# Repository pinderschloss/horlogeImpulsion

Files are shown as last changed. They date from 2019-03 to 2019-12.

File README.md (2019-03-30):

https://bit.ly/2SEGcSN
# horlogeImpulsion
Contrôleur d'horloge fille à impulsion, en subsitution à une horloge mère. Permet, selon les configurations, le pilotage par une boitier autonome alimenté par pile, batterie, ou port USB.
Il est conçu autour:
- d'un programme dont les options de compilation doivent être adaptées au besoin,
- et d'un circuit imprimé unique sur lequel l'implémentation des composant varie en fonction des besoins.

Convient (testé) pour:
- Brillié 'rosace 10 ohms' à impulsions électriques alternées (2 impulsions par minute) sur 2 piles AA, soit en pas simples toutes les 30secondes, soit en double pas toutes les minutes.
- Bodet '24V' à impulsions électriques alternées (1 impulsion par minute) sur alimentation USB.
- IBM '24V' à impulsions électriques non-alternées sur alimentation USB. 

Devrait convenir pour:
- Tout type d'horloge fille à impulsions alternée ou non, nécessitant une tension entre 2 et 36V, sur tout type d'alimentation entre 2 et 5V.

## Description :
Le controleur se base sur:
- une base de temps électronique (RTC : real time clock).
- une alimentation - n’importe quelle source délivrant entre 3V et 5V continu.
- un microcontroleur ATTinyx5 (25, 45 ou 85; testé uniquement sur Attiny85)

## Composants :
1.	Platine
2.	Microcontrôleur ATTINYx5-20PU (testé sur ATTINY85-20PU)
3.	Module RTC (la pile est facultative et ne sert pas) - testé sur un DS3231
4.	Boitier de pile ou alimentation microUSB
5.	Bouton poussoir de réglage
Selon les versions/besoin:
6.	Interrupteur ON/OFF 
7.	Pont en H et bornier pour relier la platine à l’horloge (avec sa résistance de 10 ohms)
8. transistor et bornier de sortie directe
9. bornier de sortie pour contrôle d'un pont H extérieur
10. Module convertisseur (élévateur) de tension vers la tension de fonctionnement de l'horloge (généralement 18V ou 24V)

## Brancher la platine à l’horloge :
### Brillié (10Ohms) 
-  Eteindre le contrôleur (interrupteur ON/OFF) ou bien débrancher l'alimentation
-  Relier bornes de sortie de la platine  avec les bornes d’entrée de l’horloge (2 fils). Laisser la résistance de 10ohm qui relie les deux bornes à vis .
-  Fixer l’ensemble des éléments au dos de l’horloge en assurant que l’on puisse manipuler : 
   -  les 2 interrupteurs (ON/OFF et le bouton poussoir AVANCE),
   -  le bouton,
   -  le boitier de piles.
-  Rallumer le contrôleur (interrupteur ON/OFF) ou bien brancher l'alimentation
-  Appuyer plusieurs secondes sur le bouton AVANCE, pour faire avancer l’aiguille des minutes de quelques minutes.
-  Quelques après avoir relâché le bouton AVANCE, regarder la position de l’aiguille des minutes :
   -  Si elle est alignée sur un point du cadran indiquant les minute, passer à l’étape de mise à l’heure.
   -  Sinon, elle se trouve au milieu entre deux points de minutes. Recommencer cette étape de branchement en inversant les deux fils qui relient la platine à l’horloge.

### Horloges à impulsions alternées
- Si la tension requise est supérieure à la tension d'alimentation, relier le pont en H externe (4 fils: VP, GND, S1 et S2) et brancher l'horloge comme une Brillié (10ohms) depuis le pont en H.
- Sinon (pas d'élévation de tension), procéder comme pour les Brillié (10ohms)

### Horloges à impulsions monopôlaires (pas d'inversion de polarité)
Ces horloges peuvent avoir 2 ou 3 fils. La platine peut elle-même comporter un bornier double ou triple. Toutes les combinaisons sont possibles. Attention: ne pas considérer ni connecter le fil de masse de l'horloge.
- S'il y a deux fils: en connecter un sur le connecteur marqué "rouge" (vers le coin de la platine) et l'autre fil dans l'autre bornier (n'importe lequel s'il y en a deux)
- S'il a 3 fils: le fil rouge doit être connecté à la platine sur le connecteur marqué "rouge" (vers le coin de la platine), et les deux autres soit ensemble soit séparemment dans le ou les les autres connecteurs du borniers.
- Lorsqu'on appuie sur le bouton poussoir AVANCE, vérifier que l'aiguille avance bien d'une minute.

## Mettre à l’heure l’horloge
-	Eteindre le contrôleur (interrupteur ON/OFF)
-	Approcher de l’heure réelle à la main, sans la dépasser (environ cinq à dix minutes avant l’heure réelle), en agissant directement sur le mécanisme. Pour cela agir directement sur le mécanisme d'entrainement (dépend du mécanisme - en général on peut l'avance et le reculer avec les deux mains ou tournevis), ou bien allumer le controleur et appuyer sur le bouton AVANCE sans le relacher (la vitesse d'avancement augmente lorsqu'on reste appuyé, mais cette opération peut être un peu fastidieuse).
-  Allumer le contrôleur (interrupteur ON/OFF)
-	En appuyant sur le bouton AVANCE, faire avancer jusqu’à afficher l’heure actuelle. A ce stade, l’horloge a de 0 à 59 secondes de retard.
-	Surveiller le nombre de secondes de l’heure réelle. Entre 55s et 59s, appuyer sur le bouton AVANCE. L’aiguille des minutes passe à la minute suivante: relacher immédiatement.

Note : 
-	 Ce réglage s’effectue de la même façon quel que soit le mode choisi (mode 60 : minute entière, ou mode 30 : demi minute), et se fait sur les minutes entières uniquement.
-	Compte tenu du temps variable de prise en compte de l’appui sur le bouton AVANCE, il est difficile d’obtenir une synchronisation meilleure que 2 secondes.

## Choix du mode de fonctionnement :
Identifier les caractéristiques de l'horloge:
- voltage
- nombre de fils
- type de 'moteur': 
  - électro-aimant et crabot sur roue crantée = impulsions non-alternées (les impulsion alternées fonctionneront aussi)
  - moteur type pendule et mécanisme d'échapement = impulsions alternées
  - moteur type Lavet (pas-à-pas 2 pas) = impulsions alternées
- période : temps minimal entre deux états stables de l'entrainement: 30 secondes ou 60 secondes. A tester à la main.

Attention: pour les horloges de période différentes de 30s ou 60s, il faudra modifier le programme (et pas seulement les options de compilation).

Pour les horloges dont la période est 30s:
- choisir si on souhaite un mouvement toutes les 30 secondes, ou un double mouvement toutes les 60s
- Ce choix n’a pas d’influence sur la précision de l’horloge. Le bruit produit par l’avancée de l’aiguille est différent selon le mode (un ‘clac’, ou bien un double ‘clac’ mais deux fois moins fréquent).

## Préparation de la platine
Voir le BOM.txt

## Programmation du microcontroleur :
- Le code est disponible à l’adresse suivante https://github.com/pinderschloss/horlogeImpulsion/
- Platine et code sont prévus pour fonctionner avec les microcontrôleurs ATTINYx5-20PU (x5 : 25 ou 45 ou 85) d’ATMEL. La consommation d'énergie est réduite autant que possible par une utilisation du mode sommeil autant de possible.
- La programmation du microcontrôleur peut se faire par une carte arduino par exemple (chercher Arduino ISP).
- Attention le microcontroleur ne peut pas être programmé en place sur le circuit imprimé.
- Le code est adaptable pour fonctionner avec des horloges nécessitant des signaux différents, en commentant ou décommentant les options de compilation.

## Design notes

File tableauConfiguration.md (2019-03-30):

# Configuration matérielle et logicielle

Cette partie détaille les différences entre les configurations matérielles pour la platine. La partie commune à toutes les platines est décrite dans BOM.txt. Ce fichier comprend aussi les différents éléments spécifiques listés ci-dessous, mais sans explications.

## Tensions:
Alimentation du module: **Vc** (doit être comprise entre 3V et 5V)
Tension de fonctionnement de l'horloge: **VP** (doit être comprise entre Vc et 36V)

- Si **VP** = **Vc** : pas de module élévateur de tension
- Si **Vc** < **VP** :  prévoir module élévateur de tension *x-tension*

## Connection de l'alimentation:
Si on utilise pour une alimentation qui se termine par deux fils (par exemple un boitier à piles), il faut installer un bornier d'alimentation:
- En général utiliser un bornier double (**GND** / **Vc**),
- Dans le cas d'une horloge à impulsions alternées avec **VP** > **Vc**, prévoir un bornier triple.

Si on utilise une alimentation avec un connecteur microUSB mâle et le module élévateur de tension *x-tension*, il n'y a rien à prévoir.

Pour tous les autres cas, prévoir un raccordement spécifique de l'alimentation à **GND** / **VC**.

## Commande de puissance
Pour les horloges à impulsions monopolaires, on peut au choix utiliser l'une des 3 solutions suivantes:
- Un transistor *T1*, une résistance de courant de base *R1*, et une diode de roue libre *DRL1*,
- Un pont en H :
   - Si **VP** < 15V : *pontH* soudé à la platine
   - Si **VP** < 36V : un pont en H externe (convient aussi si **VP** < 15V)
   
Pour les horloges à impulsions alternées, on doit utiliser un pont en H:
   - Si **VP** < 15V : *pontH* soudé à la platine
   - Si **VP** < 36V : un pont en H externe (convient aussi si **VP** < 15V)

## Connection à l'horloge
Si on utilise transistor *T1*: prévoir un bornier *monopolaire* double (pas 2.54mm ou bien pas 5.08 mm) ou triple (pas 2.54mm)
Si on utilise un pont en H : utiliser les connecteurs borniers du pont.
Pour les horloges Brillié "10ohms" prévoir aussi une résistance de 10 ohms.

## Economie d'énergie
Si:
- on souhaite une alimentation autonome (pile, batterie) et non pas alimenté sur le secteur,
- et on a besoin de l'élévateur de tension, 
On peut avoir plus d'autonomie en économisant l'énergie dissipée par l'élévateur de tension au repos.

Pour cela, prévoir:
- un shunt (j'utilise une résistance d'une centaine d'ohm, un fil conviendra)
- pour les horloges à impulsions alternées: deux diodes *DS1* et *DS2*.
- pour les horloges à impulsions monopolaires: un pont de soudure sur le cavalier dans l'empreinte DS1 ou un shunt à la place de la diode *DS1*.

## Interrupteur de commande
On peut installer l'*interrupteur* pour la partie commande (**Vc**). C'est un interrupteur facultatif. S'il n'est pas installé, faire un pont de soudure sur *JP2*.

## Bouton poussoir de réglage
Si on ne souhaite pas utiliser le bouton poussoir *Reglage* prévu (soudé sur la platine par 4 points):
- ne pas l'installer
- prévoir un bouton poussoir déporté et le raccorder à la platine sur un des deux points qui sont le long du bord (**SQW**), et un des deux points qui sont près de *DRL1* (**GND**).

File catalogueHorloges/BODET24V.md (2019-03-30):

# Horloge électrique Bodet 24V
## Identification
Vue de face
Vue de dos
## Caractéristiques
Il s'agit d'un modèle à impulsions alternées toutes les 60s. Elle nécessite donc un pont en H externe.
Cette horloge peut être alimentée directement par un bloc de piles AA (2x1,5V = 3V). Sur deux accus NiMh assez vieux, elle tient **A mettre à jour**.
## Options pour le programme.
```
// ---- CONFIGURATION ----
#define alternee // Pour une horloge qui a besoin d'impulsions de polarité altérnées
#define d_pas 200  // Durée impulsion sur broche 1 pour les impulsions de même polarité
// ----      FIN      ----
```
## Suggestion de présentation
Vue de dos

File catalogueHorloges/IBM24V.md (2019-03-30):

# Horloge électrique IBM 24V
## Identification
Vue de face
Vue de dos
## Caractéristiques
Il s'agit d'un modèle à impulsions monopolaires toutes les 60s.
Elle a la particularité de disposer d'un système de mise à l'heure. Ce système n'est pas utilisé dans ce projet.
Connecter les 2 fils reliés à la bascule interrupteur ensembles ou séparement dans les emplacements **NOIR** et **BLANC** (aucune importance).
Si les aiguilles ne bougent plus à XXh59: vérifier que le fil connecté directement à la bobine est sur l'emplacement **ROUGE**.
Cette horloge peut être alimentée directement par un bloc de piles AA (2x1,5V = 3V). Sur deux accus NiMh assez vieux, elle tient **A mettre à jour**.
## Options pour le programme.
```
// ---- CONFIGURATION ----
#define d_pas 200  // Durée impulsion sur broche 1 pour les impulsions de même polarité
// ----      FIN      ----```
## Suggestion de présentation
![Vue de dos](../PHOTOS/IBM24V/.JPG)

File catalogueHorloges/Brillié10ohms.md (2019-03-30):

# Horloge électrique Brillié avec la mention 'rosace 10 ohms'
## Identification
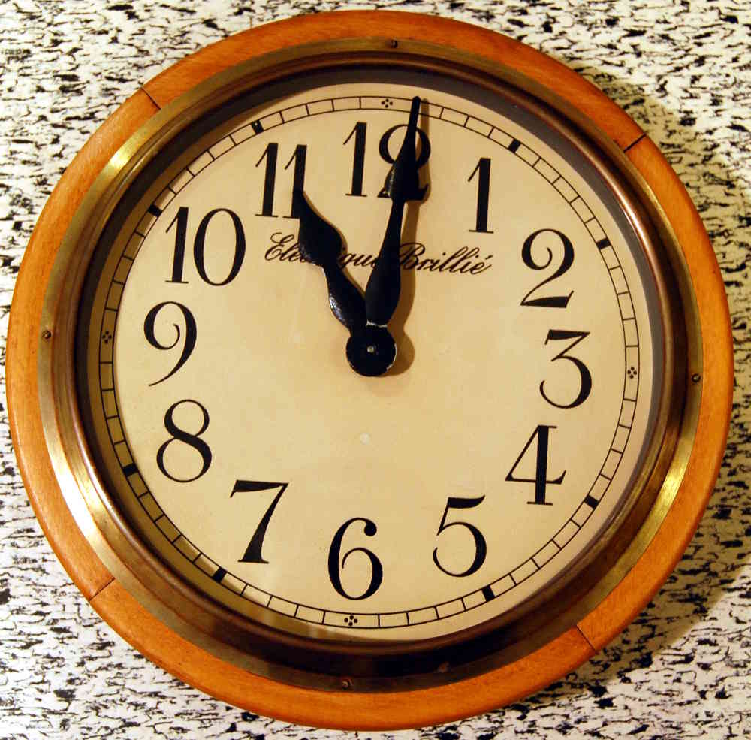
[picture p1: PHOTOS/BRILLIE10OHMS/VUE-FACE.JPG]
Vue de face

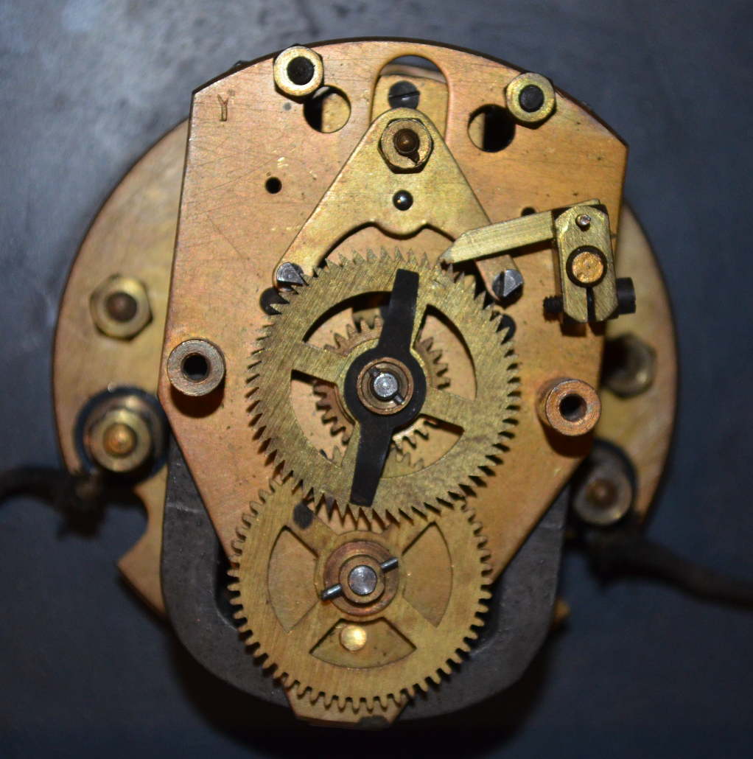
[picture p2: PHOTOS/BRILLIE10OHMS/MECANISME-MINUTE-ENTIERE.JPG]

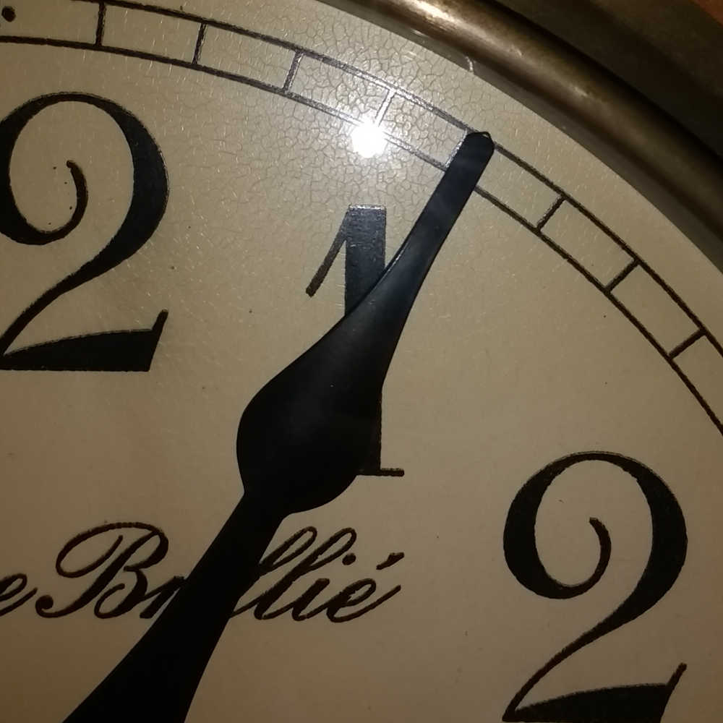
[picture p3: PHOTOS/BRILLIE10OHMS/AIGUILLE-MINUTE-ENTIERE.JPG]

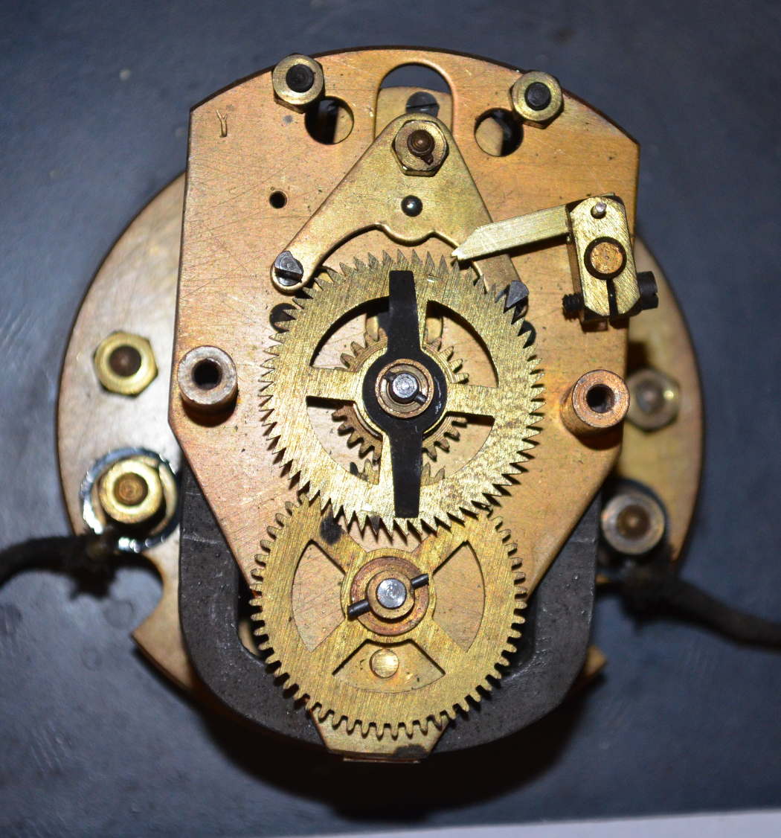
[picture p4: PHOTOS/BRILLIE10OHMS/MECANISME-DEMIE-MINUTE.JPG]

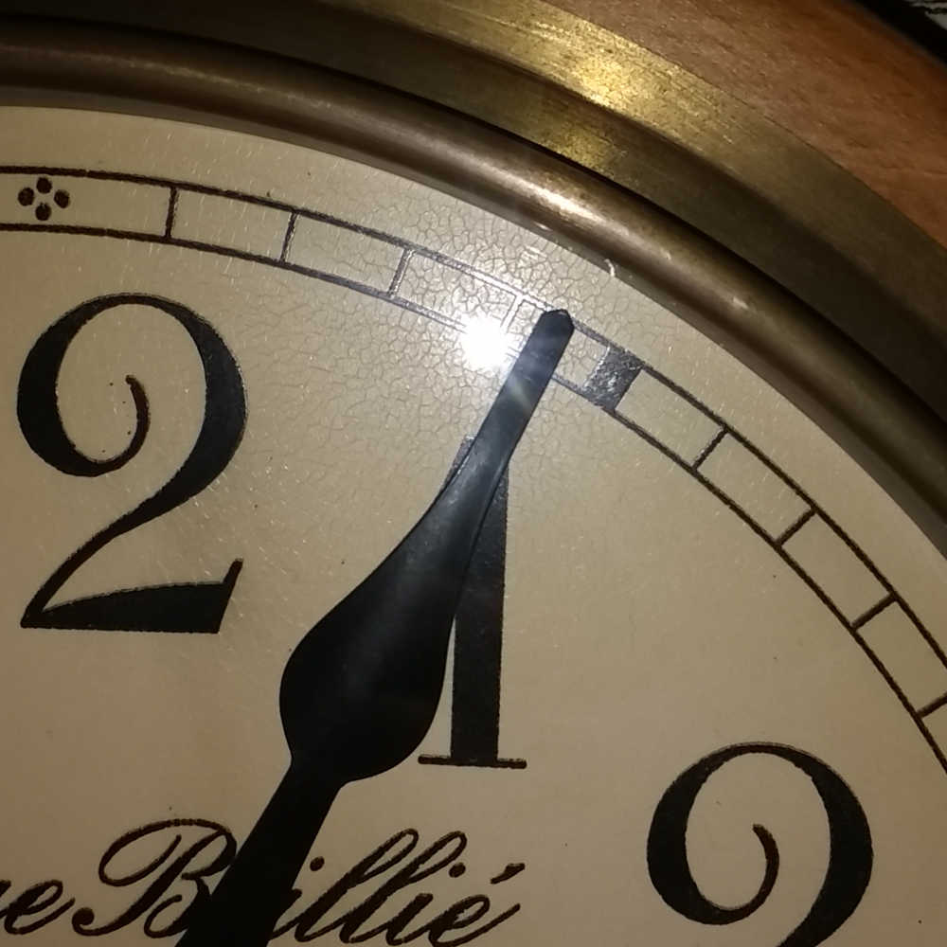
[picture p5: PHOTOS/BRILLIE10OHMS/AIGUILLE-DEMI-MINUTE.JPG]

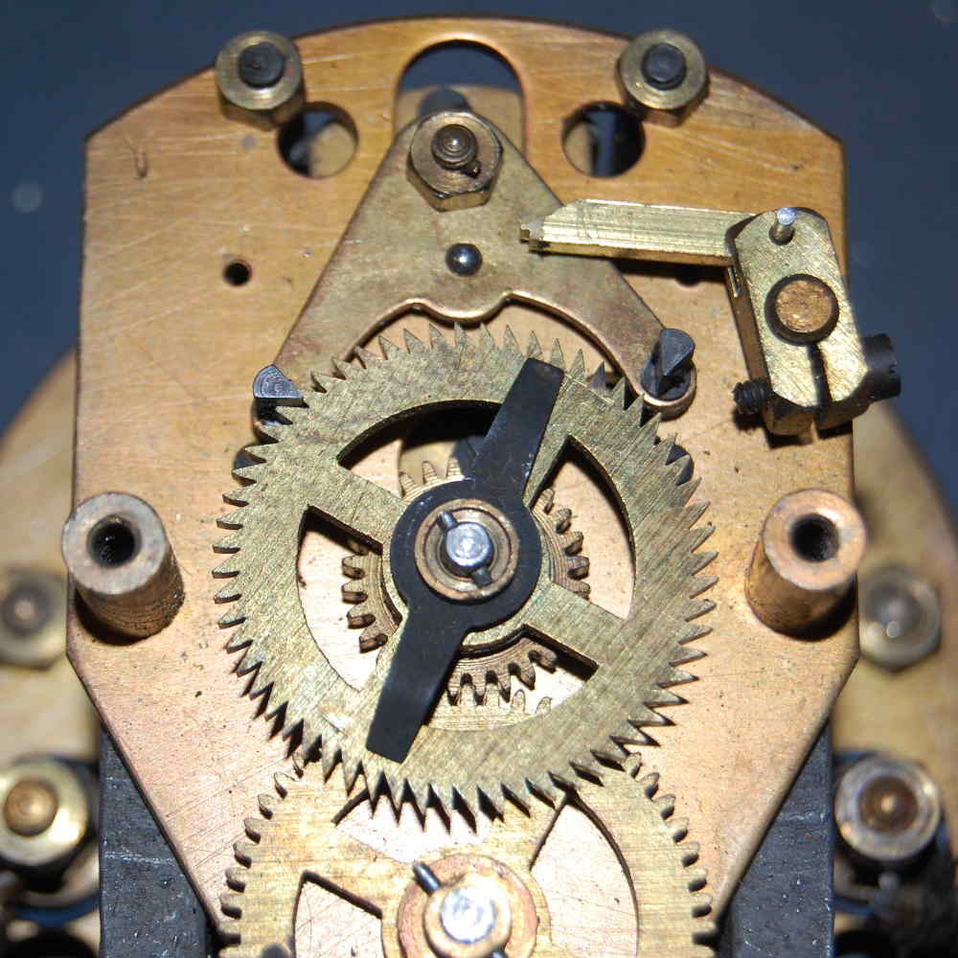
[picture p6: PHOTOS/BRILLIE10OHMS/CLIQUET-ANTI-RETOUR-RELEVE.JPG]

## Caractéristiques
Il s'agit d'un modèle à impulsions alternées toutes les 30s.
Cette horloge peut être alimentée directement par un bloc de piles AA (2x1,5V = 3V). Sur deux accus NiMh assez vieux, elle tient **A mettre à jour**.
## Options pour le programme.
On peut utiliser les réglages suivants pour le mode de fonctionnement en double pas
```
// ---- CONFIGURATION ----
#define alternee // Pour une horloge qui a besoin d'impulsions de polarité altérnées
#define pas30 // Pour une horloge dont le pas correspondant à une impulsion est de 30s
#define doublepas // Pour une horloge dont le pas est 30s, génère plutôt 2 impulsions rapprochées toutes les 60s 
#define d_pause 100 // Durée pause entre 2 impulsions alternées en millisecondes
#define d_pas_1 8  // Durée impulsion sur broche 1 pour les impulsions alternées
#define d_pas_2 10  // Durée impulsion sur broche 2 pour les impulsions alternées
// ----      FIN      ----
```
Pour une impulsion toutes les 30 secondes (temps plus important pour le pas 1 pour mieux aligner l'aiguille):
```
// ---- CONFIGURATION ----
#define alternee // Pour une horloge qui a besoin d'impulsions de polarité altérnées
#define pas30 // Pour une horloge dont le pas correspondant à une impulsion est de 30s
#define d_pas_1 10  // Durée impulsion sur broche 1 pour les impulsions alternées
#define d_pas_2 10  // Durée impulsion sur broche 2 pour les impulsions alternées
// ----      FIN      ----
```
## Suggestion de présentation
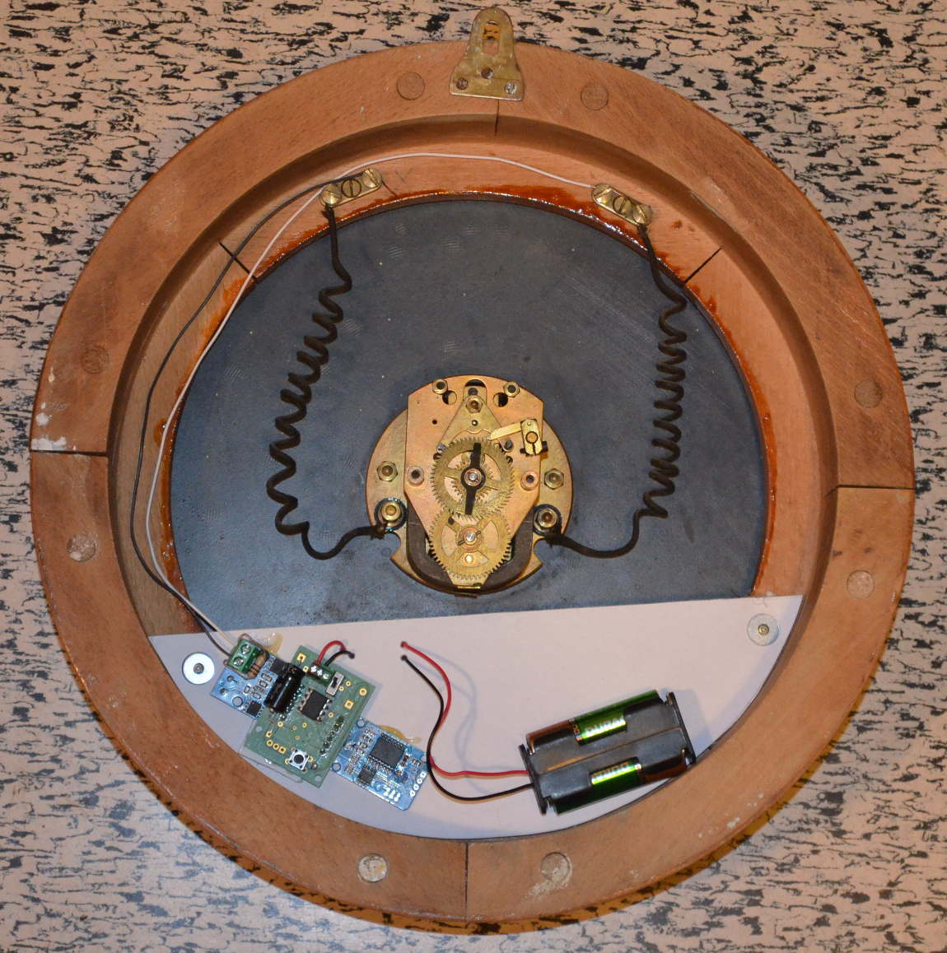
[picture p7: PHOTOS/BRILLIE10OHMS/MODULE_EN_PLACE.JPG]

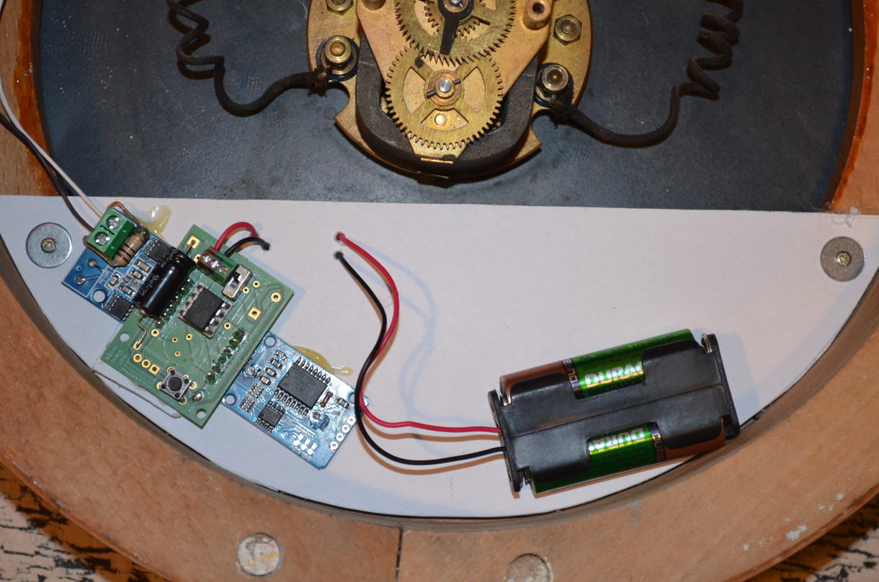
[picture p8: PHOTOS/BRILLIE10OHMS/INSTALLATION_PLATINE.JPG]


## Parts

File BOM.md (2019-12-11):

Le projet a été développé avec le matériel suivant (commum à toutes les versions) :
-  1x ATTINY85-20PU (version DIP8, ATTINY25 et ATTINY45 conviennent aussi)
-  *RTC*: 1x module assemblé DS3231 (Real Time Clock de Maxim Integrated) :
   - Un autre module RTC avec alarmes (**SQW**) devrait convenir.
   - La diode DEL a été supprimée pour économiser l'énergie.
   - Le support de pile a été supprimé pour économiser la place.
- 1x circuit imprimé dédié:
   - Il est recommandé d'utiliser la dernière version.
   - Ne pas utiliser les versions antérieures à la V5.

Suivant les versions (se référer à tableauConfiguration.md pour les explications):
-  *C* : 1x condensateur radial, diamètre 5mm (facultatif, valeur peu importante). Peut-être remplacé par un autre format.
-  *monopolaire* : 1x bornier pas 2.54mm avec 2 ou 3 bornes, ou bien un bornier pas 5.08mm à 2 bornes
-  *VPGNDVc* : 1x bornier pas 2.54mm avec 2 ou 3 bornes
-  *pontH* 1x pont en H sur une breakout board. Ce pont est basé sur un L9110S, limité à 15V.
   - Tout autre pont en H doit convenir, notamment externe.
   - La diode DEL a été supprimée pour économiser les piles.
   - Le bornier inutile a été supprimé pour éviter des confusions au moment du montage
-  *Reglage*: 1x interrupteur momentané (à poussoir)
-  *interrupteur* : 1x interrupteur à glissière (bistable)
-  *x-tension* : 1x module élévateur de tension
-  *ENABLE x-tension* : 1x résistance plutôt faible (par exemple 100 ohms ou moins) pour relier la patte ENABLE de l'élévateur de tension à la commande d'impulsion
-  *R1* : 1x résistance d'environ 1200 ohms
-  *T1* : 1x transistor NPN en package TO-90, par exemple BD259. Tout autre NPN devrait convenir s'il supporte la tension **VP**, et que ses pattes peuvent être soudées à la bonne place.
-  *DS1* et *DS2* : 2x diodes standard type 1N4001
-  *DRL1* : 1x diode standard type 1N4001
-  1x support de pile 2xAA
-  1x alimentation microUSB

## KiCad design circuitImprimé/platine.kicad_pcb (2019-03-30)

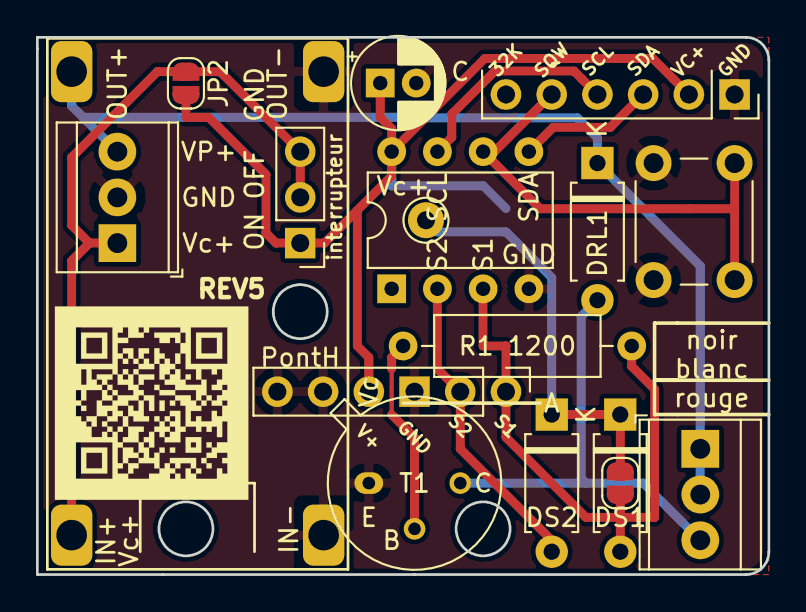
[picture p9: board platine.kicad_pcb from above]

Board: 2 copper layers, 40.6 x 29.8 mm, 18 parts (1 on the bottom side), 12 nets.

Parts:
Alimentation1: bornier 3x2.54; TerminalBlock_TE_282834-3_1x03_P2.54mm_Horizontal
C: condensateur; CP_Radial_D5.0mm_P2.00mm
DRL1: Roue libre; D_A-405_P7.62mm_Horizontal
DS1, DS2: DIODE; D_A-405_P7.62mm_Horizontal
JP2: alim_controle_permanente; SolderJumper-2_P1.3mm_Open_RoundedPad1.0x1.5mm
JPS1: monoP; SolderJumper-2_P1.3mm_Open_RoundedPad1.0x1.5mm
Microcontroleur1: ATtiny85-20PU; DIP-8_W7.62mm
PontH: Fiches2.54; connecteurPontH
R1 1200: Ibase T1; R_Axial_DIN0309_L9.0mm_D3.2mm_P12.70mm_Horizontal
RTC: fiches2.54; RTCDS321surPINHEADER
Reglage: Inter-pousser; SW_PUSH_6mm_H4.3mm
SW1: Inter-controle; PinHeader_1x03_P2.54mm_Vertical
T1: NPN; TO-39-3_Window
U1: USB-x-tension; USB-x-tension-module
monopolaire: bornier 3x2.54; TerminalBlock_TE_282834-3_1x03_P2.54mm_Horizontal
x-tension ENABLE: enable-x-tension; Pin_D1.0mm_L10.0mm
x-tension-permanent: x-tension-permanent; SolderJumper-2_P1.3mm_Open_RoundedPad1.0x1.5mm

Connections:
/Reveil: Microcontroleur1.6, RTC.5, Reglage.1
/SCL-INT0: Microcontroleur1.7, RTC.4
/SDA: Microcontroleur1.5, RTC.3
/VP+: Alimentation1.3, DRL1.1, U1.3, monopolaire.1, monopolaire.2
/Vc+: C.1, JP2.2, Microcontroleur1.8, PontH.4, RTC.2, SW1.1, x-tension-permanent.2
GND: Alimentation1.2, C.2, Microcontroleur1.4, PontH.3, PontH.5, PontH.6, RTC.1, Reglage.2, T1.1, U1.2
unnamed: Alimentation1.1, JP2.1, SW1.2, SW1.3, U1.1
unnamed: DRL1.2, T1.3, monopolaire.3
unnamed: DS1.1, DS2.1, JPS1.1, x-tension ENABLE.1, x-tension-permanent.1
unnamed: R1 1200.1, T1.2
S1: DS1.2, JPS1.2, Microcontroleur1.3, PontH.1, R1 1200.2
S2: DS2.2, Microcontroleur1.2, PontH.2

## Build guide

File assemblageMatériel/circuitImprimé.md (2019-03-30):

# Circuit imprimé
## Fichiers KICAD
Voir le répertoire de fichiers.
## Fabrication
On peut les commander sur [AISLER](https://aisler.net/p/MEIFVCUL), par 3 pour une dizaine d'euros (fabriqués en Allemagne). La finition est très bonne et les délais assez courts (une semaine environ).

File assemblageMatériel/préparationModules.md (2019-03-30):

# Préparation des modules
## Module pont en H
### Où le trouver
De très nombreux sites en lignes proposent ces modules, importés de Chine. Chercher: module L9110
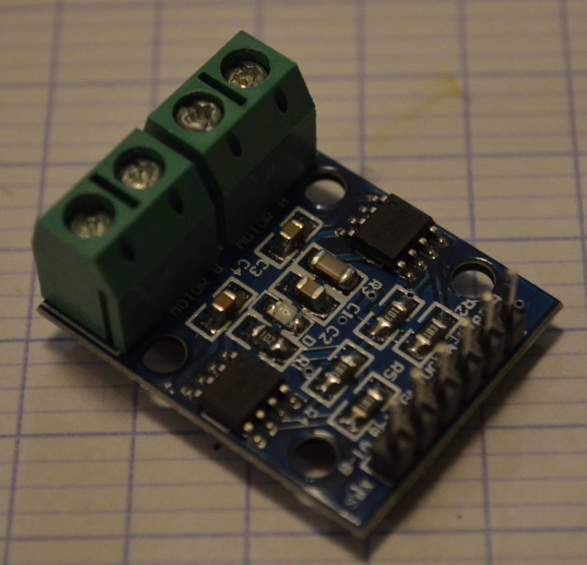
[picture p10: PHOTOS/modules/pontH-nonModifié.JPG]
module pont en H non modifié

### Le préparer
 - Pour ne pas gaspiller d'énergie, supprimer la diode DEL marqué D1 avec le fer à souder.
 - Pour ne pas avoir d'erreur au montage, dessouder le bornier du coté non utilisé.
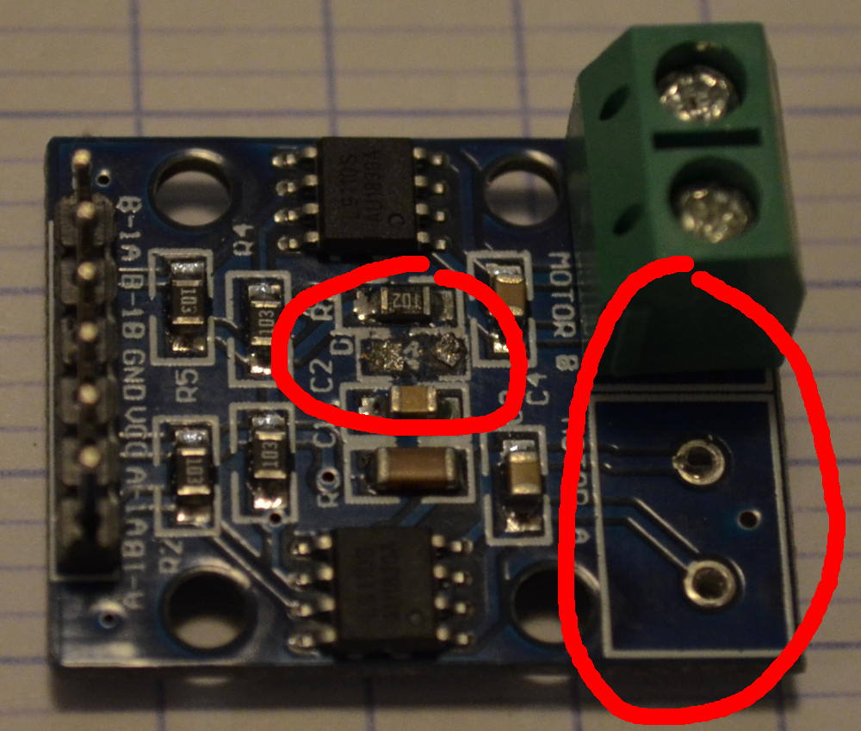
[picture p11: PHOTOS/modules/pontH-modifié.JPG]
module pont en H modifié

## Module RTC
### Où le trouver
De très nombreux sites en lignes proposent ces modules, importés de Chine. Chercher: module DS3231
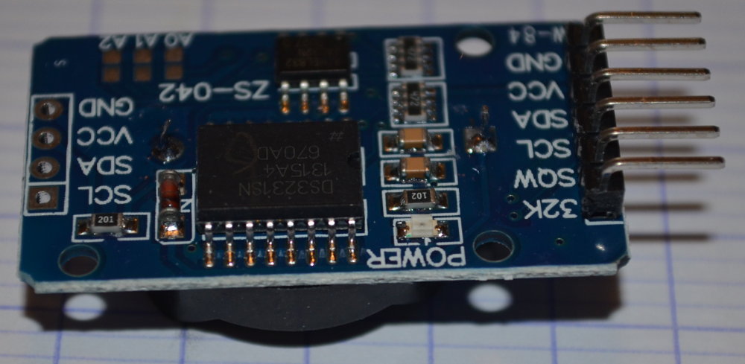
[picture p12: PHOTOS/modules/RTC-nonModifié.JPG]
module RTC non modifié

### Le préparer
 - Pour ne pas gaspiller d'énergie, supprimer la diode DEL marqué power avec le fer à souder.
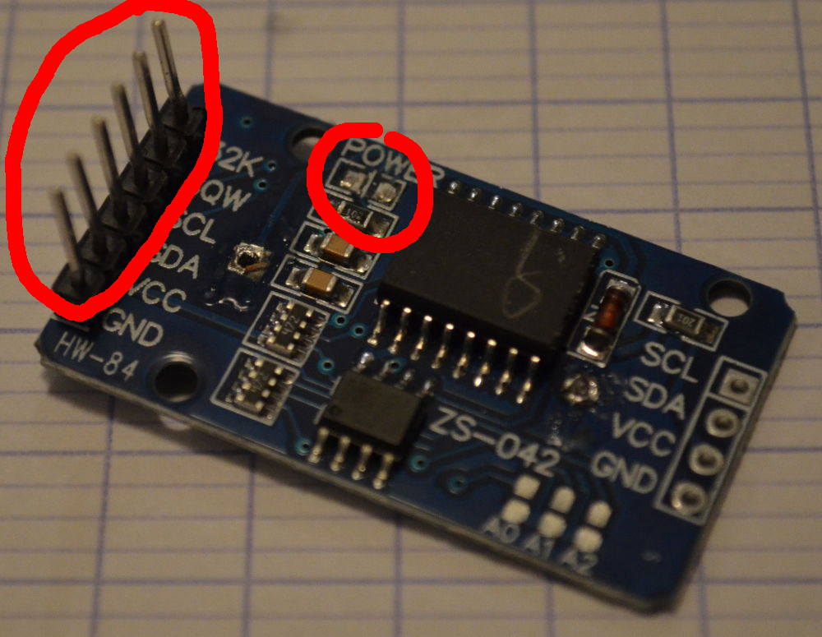
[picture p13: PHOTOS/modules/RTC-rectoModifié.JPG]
module RTC modifié recto

 - Pour ne pas être gêné par son volume, dessouder le support de pile. Elle n'est pas utile.
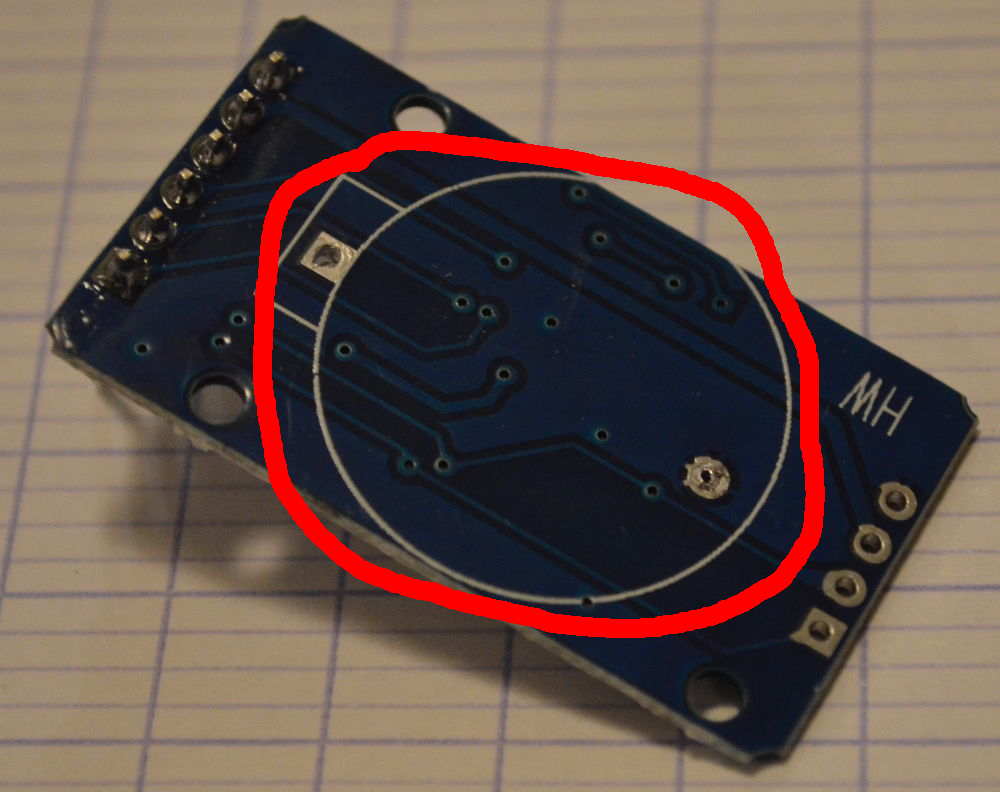
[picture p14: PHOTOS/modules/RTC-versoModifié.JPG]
module non modifié

 - Pour que le montage final ne soit pas trop encombrant, redresser les 6 connecteurs de sortie.
## Module élévateur de tension (x-tension)
### Où le trouver
De très nombreux sites en lignes proposent ces modules, importés de Chine. Chercher: booster MT3608 micro USB
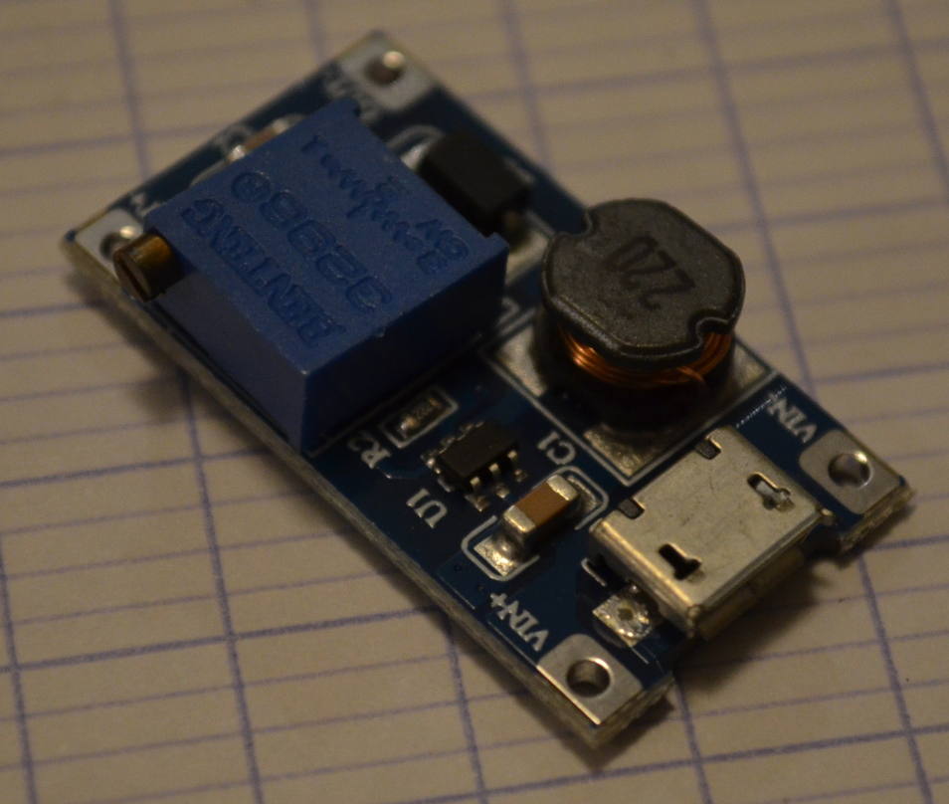
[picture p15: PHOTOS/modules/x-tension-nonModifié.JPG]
module x-tension non modifié

### Le préparer
Régler d'abord la tension de fonctionnement:
 - Relier le module à l'alimentation prévue pour le montage (**VIN+** et **VIN-**),
 - Relier un voltmètre à la sortie (**OUT+** et **OUT-**),
 - A l'aide d'un petit tournevis sur le potentiomètre bleu régler la tension de sortie selon les besoins de l'horloge (par exemple 24V).
Pour ne pas gaspiller d'énergie lors d'une utilisation non connectée au secteur, on peut utiliser la fonction ENABLE.
Ainsi le module consomme beaucoup moins au repos: on passe de ~1 milliampère à ~1 microampère.
(voir par exemple [cet article](https://hackaday.com/2019/01/27/reworking-mt3608-boost-converters-for-lower-idle-current-draw/), ou 
directement [la fiche technique](https://www.olimex.com/Products/Breadboarding/BB-PWR-3608/resources/MT3608.pdf))
Toutefois cette manipulation n'est pas obligatoire.
 - dessouder la patte du composant en la chauffant avec la panne du fer et la soulevant avec une aiguille
 - souder cette patte 'en l'air' à un fil ou une résistance (valeur peu importante - par exemple dans les 100 ohms)
 - souder l'autre extrémité du fil (ou de la résistance) sur la platine, au point **x-tension ENABLE**
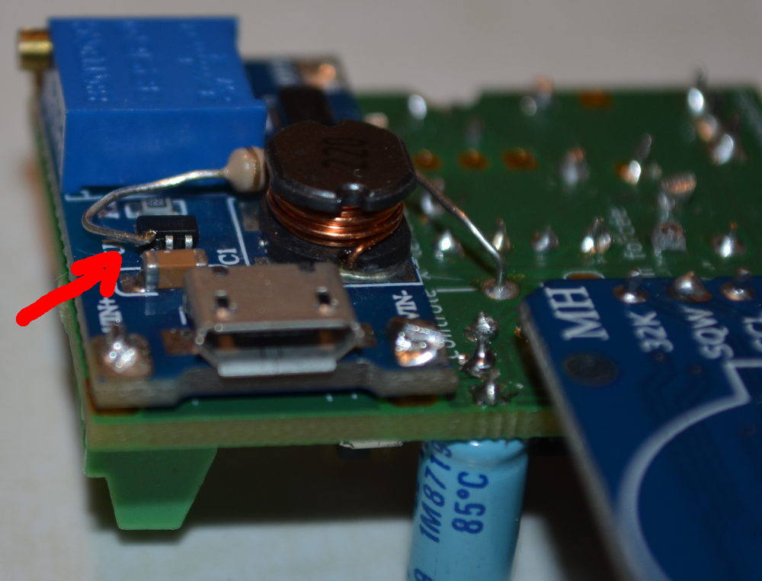
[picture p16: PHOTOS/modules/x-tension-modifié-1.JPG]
module x-tension modifié

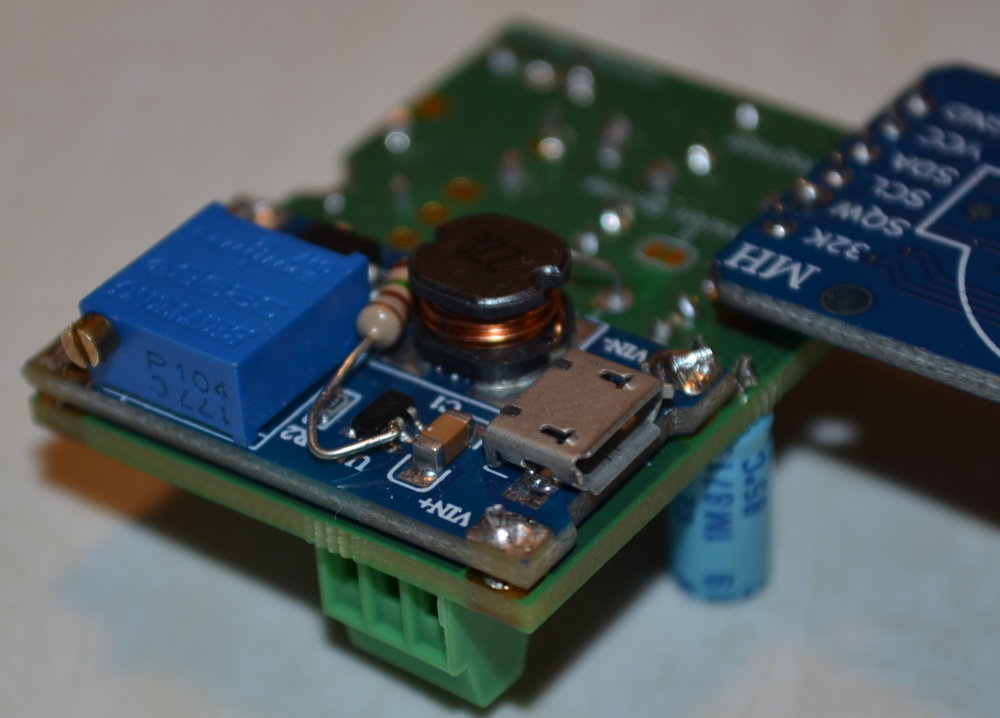
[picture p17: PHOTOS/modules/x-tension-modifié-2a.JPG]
module x-tension modifié

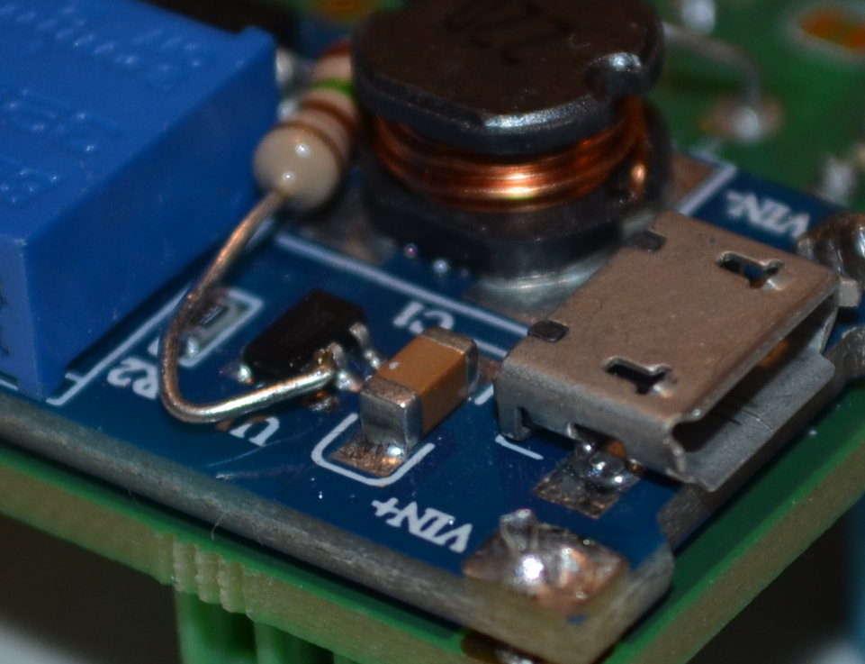
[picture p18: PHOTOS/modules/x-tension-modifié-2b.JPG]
module x-tension modifié

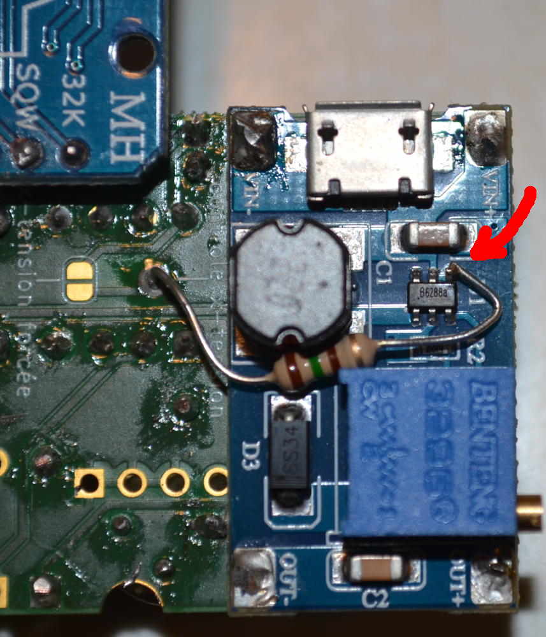
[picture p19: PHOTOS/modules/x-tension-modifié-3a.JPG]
module x-tension modifié

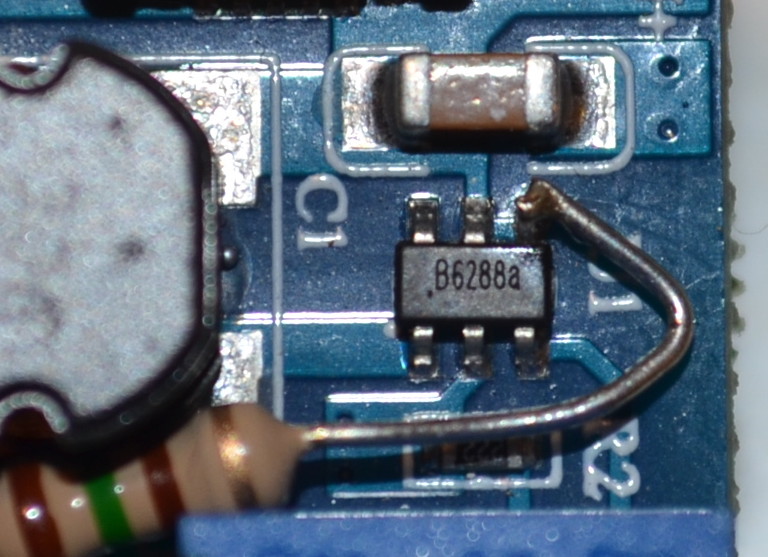
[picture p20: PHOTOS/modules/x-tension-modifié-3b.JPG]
module x-tension modifié


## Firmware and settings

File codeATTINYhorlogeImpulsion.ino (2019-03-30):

// ---- CONFIGURATION ----
// Options de compilation selon les besoins de l'horloge

//#define alternee // Pour une horloge qui a besoin d'impulsions de polarité altérnées
                 // Sinon on crée des impulsions de même polarité
                 
//#define pas30 // Pour une horloge dont le pas correspondant à une impulsion est de 30s
              // Sinon on considère que c'est 60s

#ifdef pas30
  #define doublepas // Pour une horloge dont le pas est 30s, génère plutôt 2 impulsions rapprochées toutes les 60s 
                      // Sinon comportement par défaut (1 impulsion toutes les 30s)
#endif

#ifdef doublepas
  #define d_pause 100 // Durée pause entre 2 impulsions alternées en millisecondes
#endif

#ifdef alternee
  #define d_pas_1 8  // Durée impulsion sur broche 1 pour les impulsions alternées
  #define d_pas_2 10  // Durée impulsion sur broche 2 pour les impulsions alternées
#else
  #define d_pas 200  // Durée impulsion sur broche 1 pour les impulsions de même polarité
#endif
// ----      FIN      ----

#define reveil 1 // PB1 = PCINT1 = Attiny85 pin physique 6 
                 // Reliée à la pin de réveil du module RTC et au bouton poussoir
                 // ACTIVE LOW: mise à la masse pour déclencher
                 // Ne pas utiliser sur les version de platine < V5
                 
#define broche1 3 // PB2 = Attiny85 pin physique 2
#define broche2 4 // PB4 = Attiny85 pin physique 3
// SDA et SDK non utilisées (initialisées par TinyWireM). Pour mémoire.
#define SDK    2   // PB2 = Attiny85 pin physique 7
#define SDA    0   // PB0 = Attiny85 pin physique 5

#ifndef alternee   // Dans le cas d'impulsions monopolaire, on choisit la broche 2
  #define broche broche2
#endif

#ifdef pas30
  #ifndef doublepas
    #define periode30  // C'est le seul cas où on veut une action toutes les 30s
  #endif
#endif

// Communication I2C
#include <TinyWireM.h>
// Adresse I2C real time clock (RTC) du module DS1307 ou compatible
#define DS3231_ADDR   0x68              

// Gestion des interruptions
#include <PinChangeInterrupt.h>
#include <PinChangeInterruptSettings.h>
#include <PinChangeInterruptBoards.h>
#include <PinChangeInterruptPins.h>

#define F_CPU 1000000UL  
// _delay_loop_2 = (F_CPU / 4000) * ms
#define nb_loop_2_ms 250

#include <avr/sleep.h>

 
// Routines to set and clear bits (used in the sleep code)
#ifndef cbi
#define cbi(sfr, bit) (_SFR_BYTE(sfr) &= ~_BV(bit))
#endif
#ifndef sbi
#define sbi(sfr, bit) (_SFR_BYTE(sfr) |= _BV(bit))
#endif


#ifdef alternee
bool b2=false;
#endif

void RaZRTC() {
  // réinitialise l'heure du module RTC DS3231 
  TinyWireM.beginTransmission(DS3231_ADDR); 
  // écrit une heure & date fantaisiste (mardi 23 décembre 2003, 21h53m00s)
  // cela démarre le module automatiquement s'il était bloqué
  TinyWireM.send(0x00); // Pointeur addresse HEURE
  TinyWireM.send(0x00); // 00s
  TinyWireM.send(0x53); // 53m
  TinyWireM.send(0x21); // 21h / mode 24h
  TinyWireM.send(0x03); // mardi (semaine anglaise commence un dimanche)
  TinyWireM.send(0x23); // 23
  TinyWireM.send(0x12); // décembre
  TinyWireM.send(0x03); // (20)03
  TinyWireM.endTransmission(); 
}

void RaZAlarmes() {
  TinyWireM.beginTransmission(DS3231_ADDR); 
  TinyWireM.send(0x0f); // Pointeur addresse status alarme
  TinyWireM.send(0x00); // efface toutes les alarmes (entre autres)
  TinyWireM.endTransmission();   
}

void setup() {
  cbi(ADCSRA,ADEN);                    // permute Analog to Digital converter OFF
//sbi(ADCSRA,ADEN);                    // permute Analog to Digital converter ON

  // Quelque soit le mode (alterné ou non), on s'assure de commencer avec les 2 sortie basses 
  pinMode(broche1, OUTPUT);
  digitalWrite(broche1, LOW);
  pinMode(broche2, OUTPUT);
  digitalWrite(broche2, LOW);

  pinMode(reveil, INPUT);  // SQW (interruption de réveil) est active-LOW, donc HIGH en général
                           // Idem pour le bouton poussoir

  // initialise I2C
  TinyWireM.begin();
  attend_ms(100);  // On patiente

  RaZRTC();
    // crée la(les) alarmes
  TinyWireM.beginTransmission(DS3231_ADDR); 
#ifdef periode30
  // Alarme toutes les minutes, à xx:xx:30 A1M1=0 A1M2=1 A1M3=1 A1M4=1
  TinyWireM.send(0x07); // Pointeur addresse alarme 1
  TinyWireM.send(0x30); // A1M1=0 xx:xx:30
  TinyWireM.send(0x80); // A1M2=1 xx:00:xx (valeur des minutes, ici 00, sans importance)
  TinyWireM.send(0x80); // A1M3=1 00:xx:xx (valeur des heures, ici 00, sans importance)
  TinyWireM.send(0x81); // A1M4=1 1=dimanche (valeur de jour, ici 1, sans importance)
#else
  TinyWireM.send(0x0B); // Pointeur addresse alarme 2
#endif
  // Alarme toutes les minutes, à xx:xx:00 A2M2=1 A2M3=1 A2M4=1
  TinyWireM.send(0x80); // A2M2=1 xx:00 (valeur des minutes, ici 00, sans importance)
  TinyWireM.send(0x80); // A2M3=1 00:xx (valeur des heures, ici 00, sans importance)
  TinyWireM.send(0x81); // A2M4=1 1=dimanche (valeur de jour, ici 1, sans importance)
  // Enclenchement des alarmes (addresse 0x0E)
  // EOSC=0 BBSQW=0 CONV=0 RS2=0 RS1=0 INTCN=1 (alarmes surveillées) A2IE=1 (alarme à xx:xx:00 enclenchée) A1IE=? (alarme à xx:xx:30 enclenchée): 0000011?
#ifdef periode30
  TinyWireM.send(0x07);
#else
  TinyWireM.send(0x06);
#endif
  // On arrête le 32kHz et on efface les alarmes (addresse 0x0F)
  TinyWireM.write(0x00);
  TinyWireM.endTransmission(); 

  interruptionsON();
}

void attend_ms(uint32_t n) {
  // _delay_loop_2 = 4 cycles horloge à attendre
  // s / cycle = 1 / F_CPU
  // ms / cycle = 1000 / F_CPU
  // ms / 4 cycles = 4000 / F_CPU
  // 4 cycles / ms = F_CPU / 4000
  // _delay_loop_2 = (F_CPU / 4000) * ms 
  // Attention _delay_loop_2 accepte un uint16_t (max 2^16=65536) correspondant à 262.1 ms à 1Mhz
  // C'est pour ca qu'on utilise le multiplicateur nb_loop_2_ms, défini dans les déclarations
  n=n*nb_loop_2_ms;
  _delay_loop_2( (uint16_t) n);
  n=n>>16;
  for(uint16_t i=(uint16_t) n; i>0; i--) { _delay_loop_2( 0 ); }  // _delay_looop_2( 0 ) correspond en fait à 65536
}

void identifieInterruption() {
  interruptionsOFF();
  // Lit le registre des alarmes
  TinyWireM.beginTransmission(DS3231_ADDR); 
  TinyWireM.send(0x0F); // Pointeur addresse status alarme
  TinyWireM.endTransmission();   
  TinyWireM.requestFrom(DS3231_ADDR,1);
  byte A = 0b00000011;  // Les drapeaux alarmes sont les 2 derniers bits
  A = A & TinyWireM.read();
  if (A) { // S'il n'est pas nul, c'est que c'est une alarme qui a déclenché
    avance();
    RaZAlarmes();
  } else { //sinon c'est un appui poussoir
    regle();
  }
  interruptionsON();
}

void interruptionsON() {
  // On détecte les alarmes: SQW (interruption de réveil) est active-LOW, donc HIGH en général
  attachPinChangeInterrupt(reveil, identifieInterruption, FALLING);
}

void interruptionsOFF() {
  detachPinChangeInterrupt(reveil);
}

void loop() {  // Remet le système en sommeil
    system_sleep();
}

void avance() {
  // Avance différente selon les choix à la compilation
  #ifdef doublepas
    digitalWrite(broche1, HIGH);
    attend_ms(d_pas_1);
    digitalWrite(broche1, LOW);
    attend_ms(d_pause);
    digitalWrite(broche2, HIGH);
    attend_ms(d_pas_2);
    digitalWrite(broche2, LOW);
  #else
    #ifdef alternee
    if (b2) {
      digitalWrite(broche1, HIGH);
      attend_ms(d_pas_1);
      digitalWrite(broche1, LOW);
    } else {
      digitalWrite(broche2, HIGH);
      attend_ms(d_pas_2);
      digitalWrite(broche2, LOW);
    }
    b2=!b2;
  #else
    digitalWrite(broche, HIGH);
    attend_ms(d_pas);
    digitalWrite(broche, LOW);
  #endif
#endif
  interruptionsON();
}

void regle() {
  uint32_t d = 1500;  // Temps de latence en millisecondes entre deux (groupes d')impulsion
  boolean a=true;
  #ifdef periode30
    b2=false;
  #endif
  while (a) {
    avance();
    #ifdef periode30()
      attend_ms(200);
      avance(); 
    #endif
    //delay(d);
    RaZAlarmes();
    attend_ms(d);
    if (d>300) { d *= 95;  d/= 100; }  // Si on laisse appuyé longtemps, on réduit le temps de latence

    a=!digitalRead(reveil); // Vérifie si l'utilisateur appuie encore sur le poussoir
  }
  RaZRTC();
  RaZAlarmes();
}

void system_sleep() {  // Mise en veille, en attente d'une interruption
  set_sleep_mode(SLEEP_MODE_PWR_DOWN); // sommeil le plus profond
  sleep_enable();
  sei();                               // Assure que les interruptions sortent l'ATTiny de la veille
  sleep_mode();                        // Mise en veille
  // zzz ...
  sleep_disable();                     // Sortie de la veille
  cli();                               // Réactive les interruptions
}
 

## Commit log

2019-03-30 ajout des descriptions partielles de IBM, SIMPLEX, BODET
2019-03-30 ajout du lien vers Aisler
    [platine.kicad_pcb, platine.sch]
